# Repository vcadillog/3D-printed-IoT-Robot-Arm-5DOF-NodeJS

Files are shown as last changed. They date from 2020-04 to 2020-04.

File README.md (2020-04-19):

# OPEN-SOURCE-5DOF-IOT-ROBOT-ARM

Fully developed Robot Arm with a web app for a educational purpose in robotics and programming, using an IP camera, 3D printing, Arduino and NodeJS.

## MATERIALS REQUIRED

* 3D printer
* WiFi connection.
* A computer as a Web Server (can be used a Raspberry PI) with NodeJS installed.
* IP camera.
* 5V, 5A DC Power Source.
* 5V to 3.3V Step Down converter.
* 1 ESP8266-01s, can be used another ESP8266 module based with at least 2 GPIO pins.
* 5 Servo Motors: 
  * 2 Servo Motors MG996R
  * 3 Servo Motors SG-90
* 1 PCA9685 Servo Driver 16 channels.
* Wires
* 2 resistors 330 Ohm.
* 12 M3 Allen Bolts
* 1 Protoboard 

## ASSEMBLY

For the first 2 degrees of freedom, use 4 bolts to hold each MG996R Servo motor and 4 bolts for the PCA9685.

In the image the bigger hole is to hold the PCA9685 and the small for the Servo Motor MG996R.

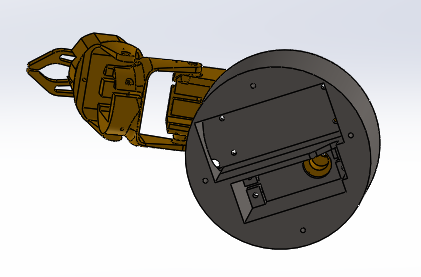
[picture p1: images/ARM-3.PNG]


The next 3 DOF can be assembled without screws only using pressure to hold the servo motors to the body.

The gripper consist of 2 pieces, one connected and holded to the servo motor and another guided by the movement and connected to the body not too tight.

## CONNECTIONS

The wire connection is made between the ESP8266 and the PCA9685 as the following image.

Default pins for Servo Motors and PCA9685 are [1,3,4,7,8], modify if you need in the arduino code.

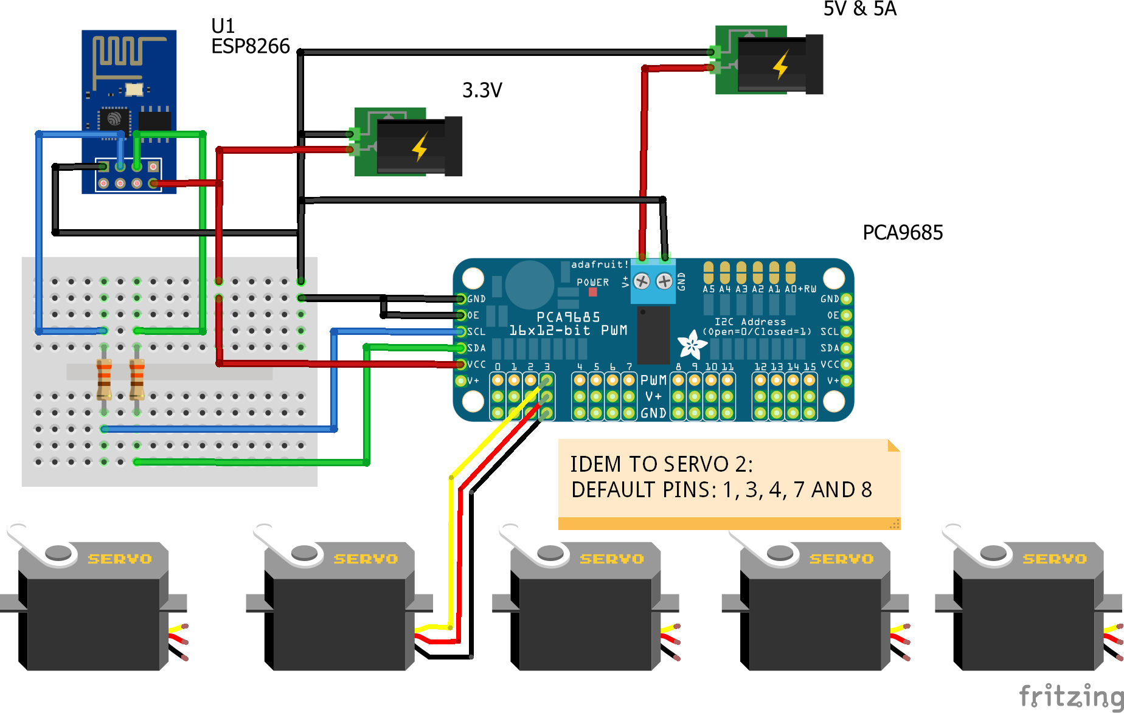
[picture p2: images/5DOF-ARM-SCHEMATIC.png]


## HOW TO USE

### Arduino code
* [1] Open the code  inside the code/arm-control/arm-control.ino . 
* [2] Set the values of you WiFi router and the Web Server URL and web socket of the Arduino code.
* [3] First uncomment the Update_Values Function inside the void loop of arduino to get the specific values of your servo motors.
* [4] Modify if required the pos0 and pos180 values to match the pulse width of your servo driver that map a movement of 0-180°.
* [5] Comment back the Update_Values after setting the values and upload the program to the ESP8266-01s.

### NodeJS code
* You have to need installed ffmpeg
* [1] Change directory in terminal to code/arm-frontend and install modules with:
  * Run npm init
  * Run npm install express
  * Run npm install node-matrix
  * Run npm install node-rtsp-stream  
* [2] Open the code inside code/arm-frontend/app.js
* [3] As the same done on the arduino code, modify your hostname with the IP of your computer and the PORT of your choice.
* [4] The IP camera use a RTSP protocol, it can't be showed in the template directly, since that modify with the RTSP direction of your IP camera, if you have an HTTP url, can be done directly modying the index.html template.

The WS port for the IP camera has to be different than the PORT declared for your webserver.

### Template
* [1] Open the code inside code/arm-frontend/client/index.html
* [2] Change the web socket direction of your RTSP camera as the same in the JavaScript code.

## RUN THE CODE
* [1] After made all the modifications to the directions change the direction of the NodeJS app and run with:
node app.js
* [2] Turn on your Robot Arm.
* [3] Then open a browser and connect to the URL choseen.

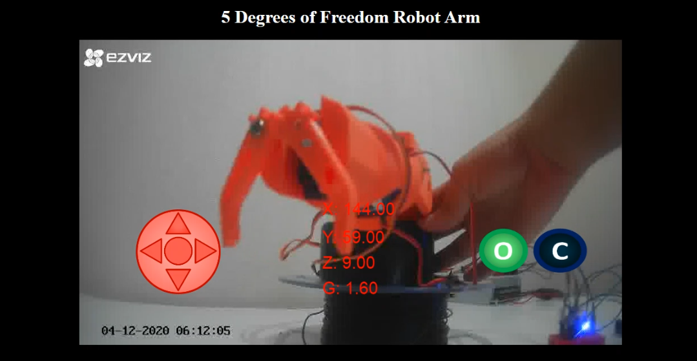
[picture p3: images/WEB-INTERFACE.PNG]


To move the Arm, use the keyboard Q,E to move the Z-axis, W,S to the Y-axis and A,D for the Z-axis; for the gripper O for open and P for close.

If the arm is moved outside the boundaries it will show invalid position since the Inverse Kinematics isn't posible to be calculated, and you have to move back to a position that is allowed.

The initial position is set as a extended arm.

## This code was based on:
* [1] Robot dynamic and Control. W. Spong
* [2] Multiplayer NodeJS game Tutorial 
https://scripterswar.com/tutorial/nodejs
* [3] Socket IO library for Arduino
https://github.com/timum-viw/socket.io-client

## To do:
* Change  the IP camera for a web camera.
* Create a circuit module for a easy connection.
* Modify the Arm Design of the base to allow connection of the ESP connection inside the arm, without external breadboard.

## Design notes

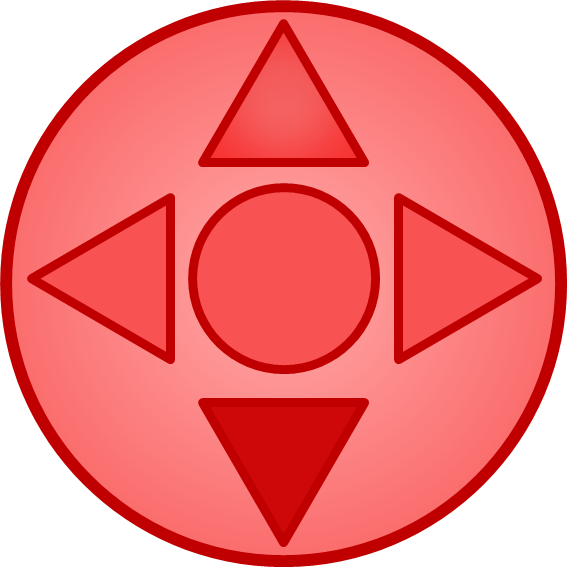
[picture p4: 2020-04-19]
code/arm-frontend/client/images/controls/joystick_y_neg.png

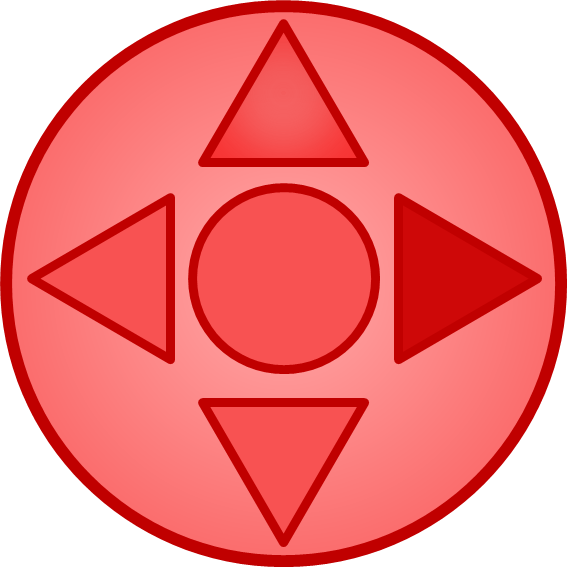
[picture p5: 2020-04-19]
code/arm-frontend/client/images/controls/joystick_x_pos.png

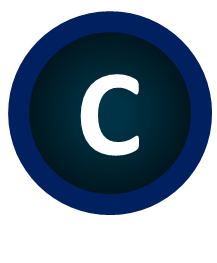
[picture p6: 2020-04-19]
code/arm-frontend/client/images/controls/close_pushed.png

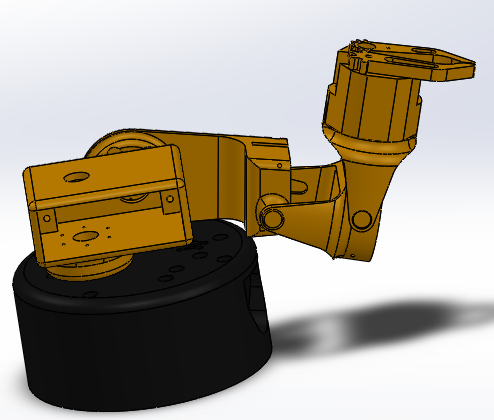
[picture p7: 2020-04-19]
images/ARM-1.PNG

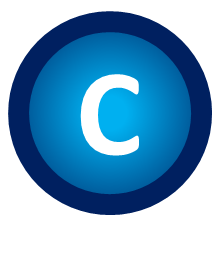
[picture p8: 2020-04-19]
code/arm-frontend/client/images/controls/close.png

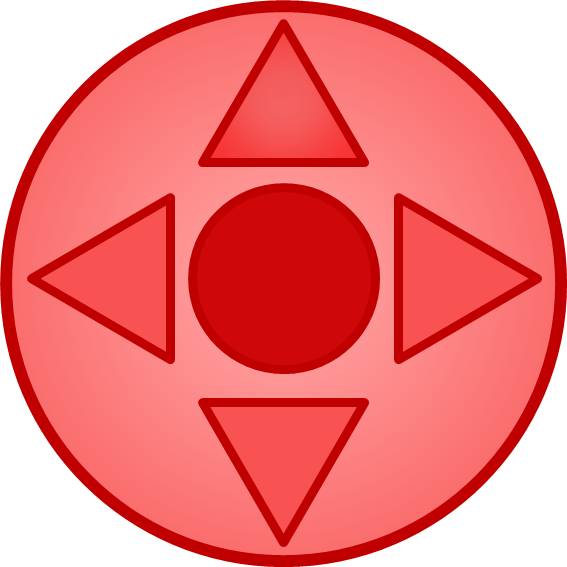
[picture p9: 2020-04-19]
code/arm-frontend/client/images/controls/joystick_z_pos.png

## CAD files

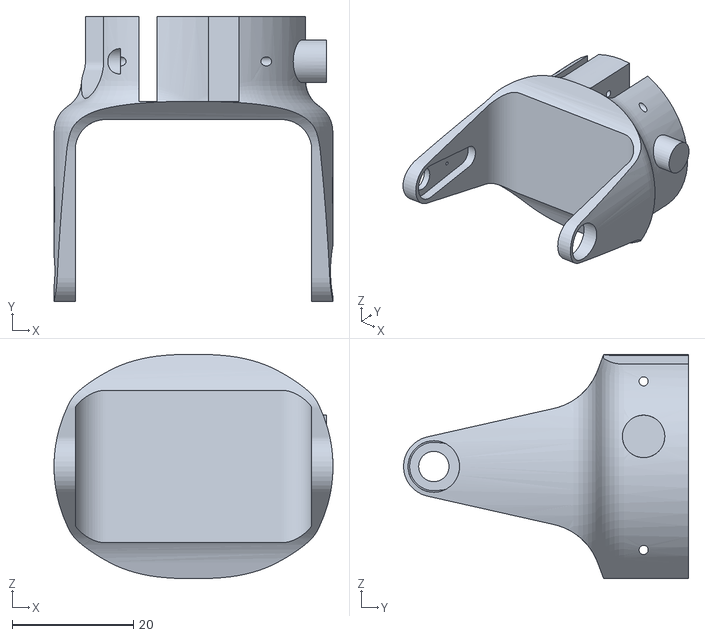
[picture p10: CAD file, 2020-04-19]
STL/DOF-4.STL
46.0 x 47.0 x 37.0

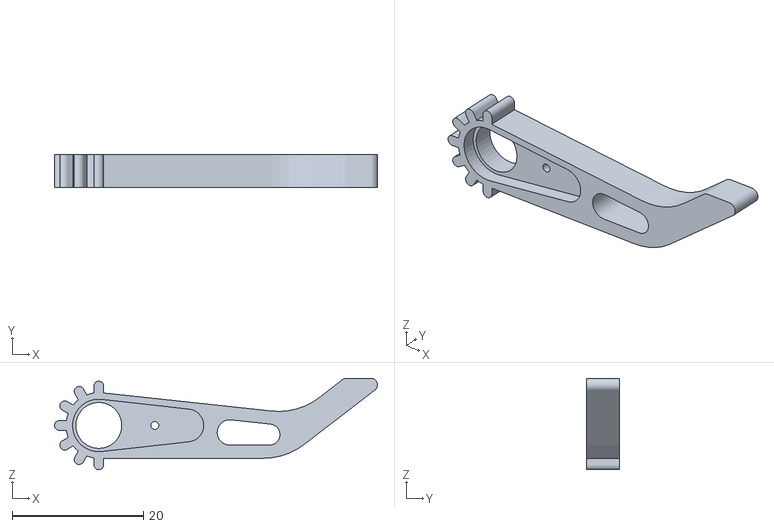
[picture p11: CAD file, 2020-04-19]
STL/GRIPPER.STL
49.2 x 5.00 x 13.9

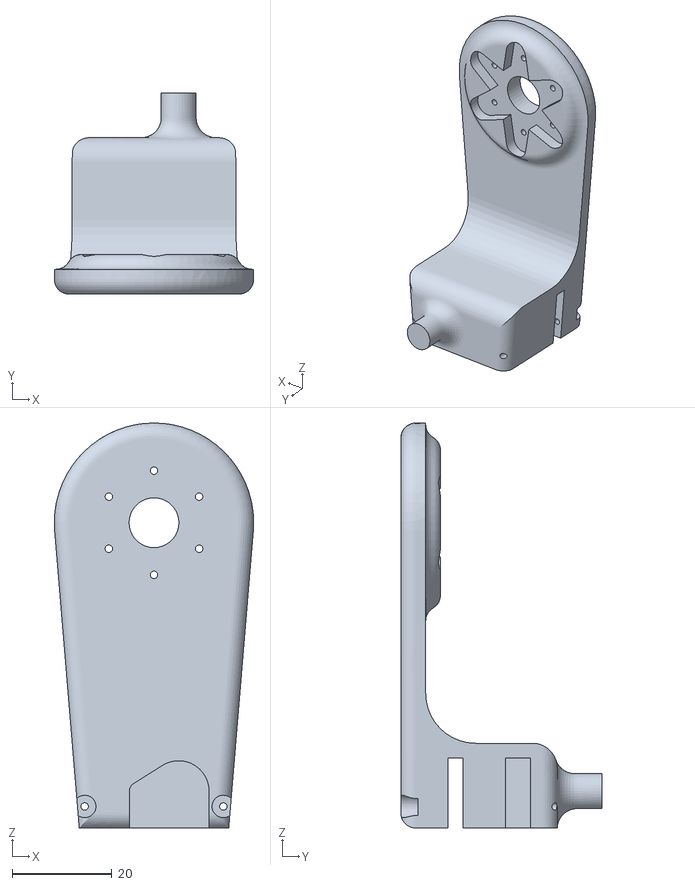
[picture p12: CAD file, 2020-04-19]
STL/DOF-3.STL
40.0 x 40.4 x 81.2

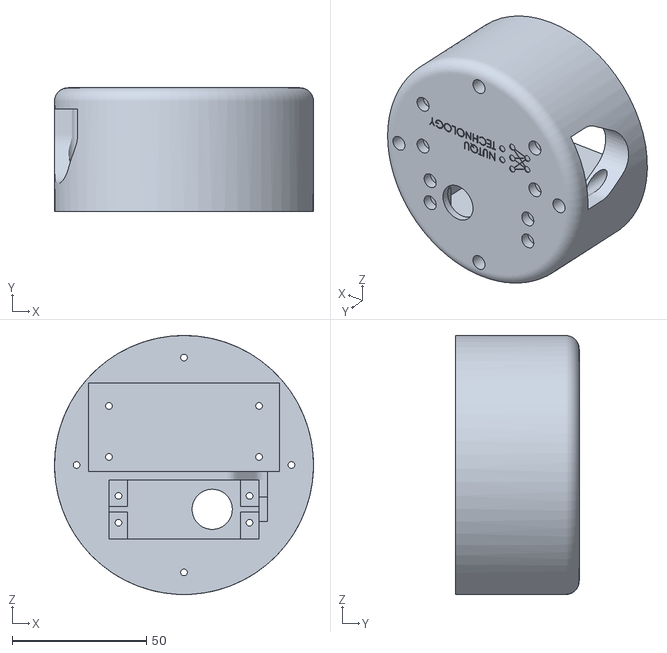
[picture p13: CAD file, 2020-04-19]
STL/BASE.STL
96.5 x 46.0 x 96.5

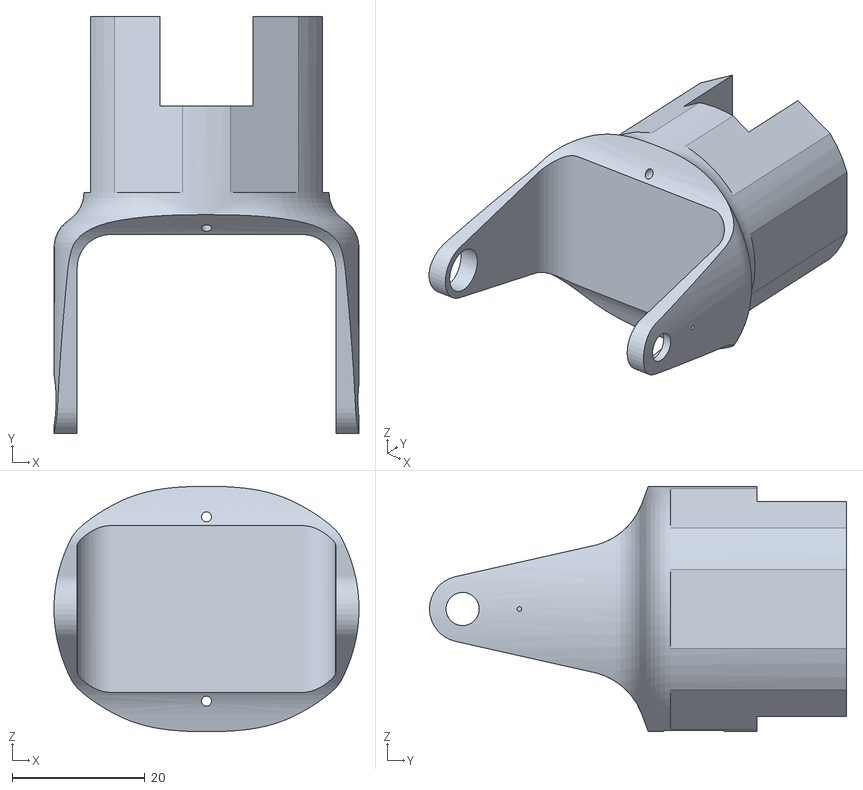
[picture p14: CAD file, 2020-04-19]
STL/DOF-5.STL
46.0 x 62.9 x 37.0

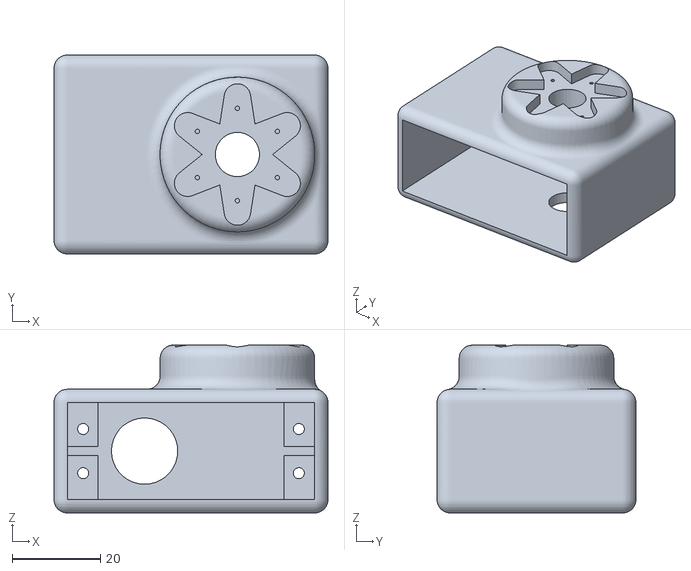
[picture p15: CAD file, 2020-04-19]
STL/DOF-2.STL
62.0 x 45.0 x 38.0

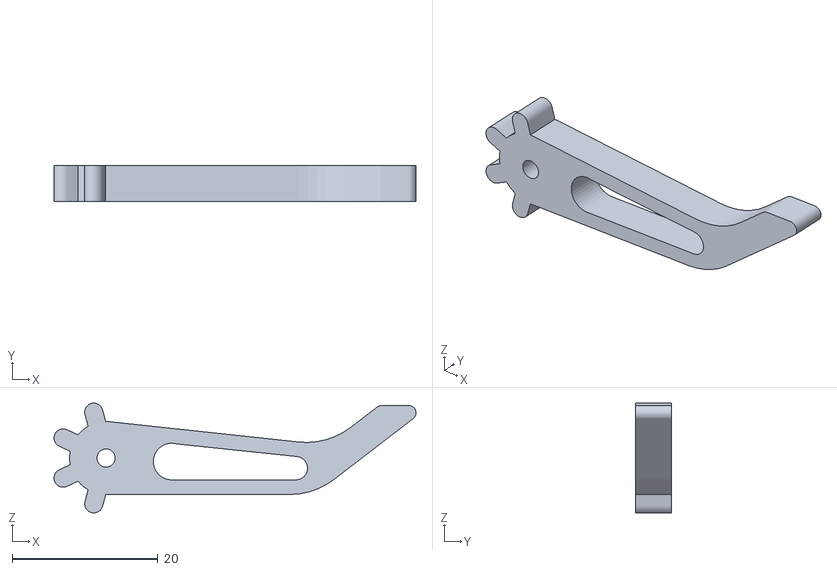
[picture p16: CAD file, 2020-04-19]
STL/GRIPPER-2.STL
49.6 x 5.00 x 15.1

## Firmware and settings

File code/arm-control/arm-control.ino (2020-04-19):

#include <Arduino.h>
#include <ESP8266WiFi.h>
#include <ESP8266WiFiMulti.h>
#include <SocketIoClient.h>
#include <Wire.h>
#include <Adafruit_PWMServoDriver.h>

#define USE_SERIAL Serial
#define SDA_PIN 0
#define SCL_PIN 2
//I2C PINS ESP8266 GPIO5 (SDA), GPIO0 (SCL)
SocketIoClient webSocket;
TwoWire I2CPCA = TwoWire();
Adafruit_PWMServoDriver servos = Adafruit_PWMServoDriver(0x40,I2CPCA);
unsigned int pos0 = 140; //pulse width for 0°
unsigned int pos180 = 650; //pulse width for 180°

float __attribute__((aligned(4))) theta[6];

const char* ssid = "Your-WiFI-SSID";
const char* password = "Your-Password";
String url =  "http://Your local web server:Port"; //example: "http://192.168.1.23:8080/"; has to match to the NodeJS app URL.
const char* web_socket_ip = "Your local web server"; // To match the url: "192.168.1.23"
const int PORT = 8080; // The port of your web server to match url variable.

void setup()
{

  USE_SERIAL.begin(115200);
  USE_SERIAL.setDebugOutput(true);
  USE_SERIAL.println();
  USE_SERIAL.println();
  USE_SERIAL.println();

  for (uint8_t t = 4; t > 0; t--) {
    USE_SERIAL.printf("[SETUP] BOOT WAIT %d...\n", t);
    USE_SERIAL.flush();
    delay(1000);
  }
  // Conectar WiFi
  
  WiFi.begin(ssid, password);
  while (WiFi.status() != WL_CONNECTED)
    delay(500);

  webSocket.on("newAngles", event);  
  webSocket.begin(web_socket_ip,PORT); //"192.168.1.23",8080

  I2CPCA.begin(SDA_PIN,SCL_PIN, 15000);
  servos.begin();
  
  servos.setPWMFreq(60);
  servos.setPWM(1,0,pos0);
  servos.setPWM(3,0,pos0);
  servos.setPWM(4,0,pos0);
  servos.setPWM(7,0,pos0);
  servos.setPWM(8,0,pos0+100);
  delay(500);  
}

void loop()
{
 //Update_Values(); //USE TO GET THE VALUES FOR YOUR SERVO MOTORS pos0 and pos180
  webSocket.loop();
  setServo(1, theta[1]);
  setServo(3, theta[2]); 
  setServo(4, theta[3]);
  setServo(7, theta[4]);  
  setServo(8, theta[5]);  
}

void Update_Values(){
    if (USE_SERIAL.available()>0){
    String stringbuffer;
    stringbuffer = USE_SERIAL.readString();
    pos0 = stringbuffer.substring(0,3).toInt();
    pos180 = stringbuffer.substring(4,7).toInt();          
    USE_SERIAL.print("Angle  0°: ");
    USE_SERIAL.println(pos0);
    USE_SERIAL.print("Angle 180°: ");
    USE_SERIAL.println(pos180);
  }   
  for (int duty = pos0; duty < pos180; duty=duty+10) {
    for(int n=0;n<16;n++)
    {
      servos.setPWM(n,0,duty);
    }   
  }
  delay(1000);
  for (int duty = pos180; duty > pos0; duty=duty-10) {
    for(int n=0;n<16;n++)
    {
      servos.setPWM(n,0,duty);
    }   
  }
  delay(1000);  
}
void event(const char * payload, size_t length) {
  USE_SERIAL.printf("got message: %s\n", payload);
  int __attribute__((aligned(4))) comma[6];
  int __attribute__((aligned(4))) point[6];
  int  counter = 0;
  int comma_counter = 0;
  int point_counter = 0;


  while (comma_counter < 5) {
    if (payload[counter] == ':') {
      point[point_counter + 1] = counter;
      point_counter++;
    }
    else if (payload[counter] == ',') {
      comma[comma_counter + 1] = counter;
      comma_counter++;
    }
    counter++;
  }
  for (int j = 1; j <= 5; j++) {
    int k = 0;
    char buf[10] = " ";
    for (int i = point[j] + 1; i <= comma[j] - 1; i++) {
      buf[k] = payload[i];
      k++;
    }
    if (buf[0] == 'n') {
      USE_SERIAL.println("Invalid");
    }
    else {
      theta[j] = atof(buf);
    }
  }
}

void setServo(uint8_t n_servo, float angle) {
  int duty;
  angle = angle * 180.0/PI;
  duty = map(angle, 0, 180, pos0, pos180);
  servos.setPWM(n_servo, 0, duty);
}
